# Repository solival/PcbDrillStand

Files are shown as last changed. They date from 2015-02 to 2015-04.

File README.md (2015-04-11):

# PCB Drill Press Stand
This is small neat drill press stand designed to use laser printer engines widely sold on ebay/aliexpress.
This project based on http://www.thingiverse.com/thing:144333 by Mark Benson design with next improvements:

- Designed for engine body sized L=35-60mm D=30mm
- Shifted base hole to center drill according new motor diameter
- Added 3x 3mm super light LED holders focused on drill working area
- Added PCB with voltage regulator and connector for standard notebook power unit (which is used for drill and light). This can be easily changed on any power source up to 24v (only connector should be changed in this case)
- Added holes in slider to mount PCB
- Added hole on left side of fixed sliding wedge for balancing spring/rubber.

Apart from that no big changes. I print gears with 40% filament and all other parts with 20% filament. Works fine.

This thing on thingiverse: http://www.thingiverse.com/thing:766712

# Photos
Drill Press Stand assembled

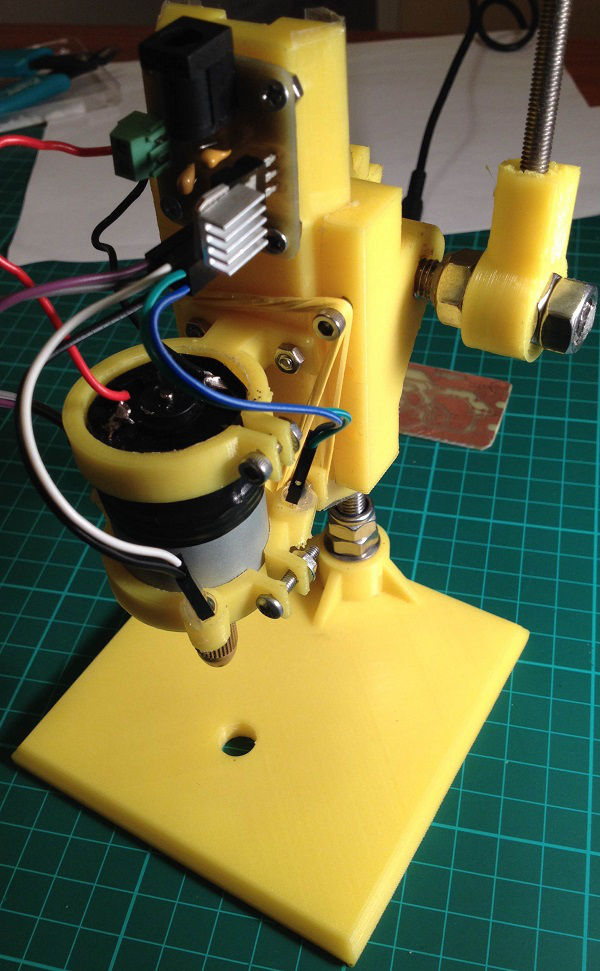
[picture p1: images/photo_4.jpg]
Drill press assembled

---

Drilling area light

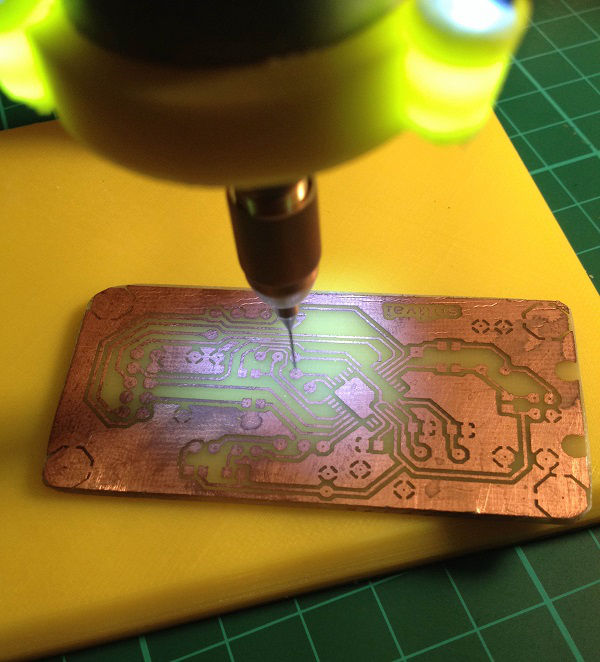
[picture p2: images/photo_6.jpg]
Drill Light

---

Assembled render front

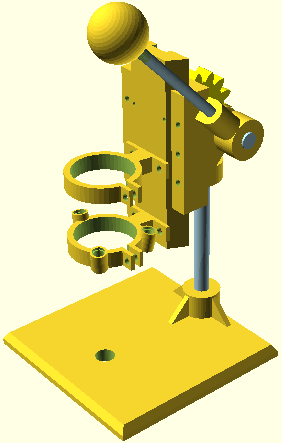
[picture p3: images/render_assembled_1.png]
Assembled Render

---

Assembled render back:

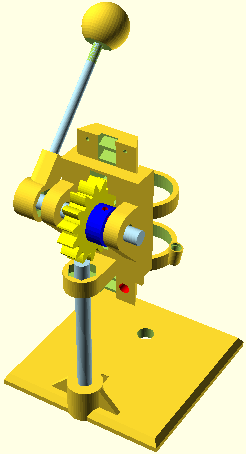
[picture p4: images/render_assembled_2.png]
Assembled Render

---

LED Light Schematics

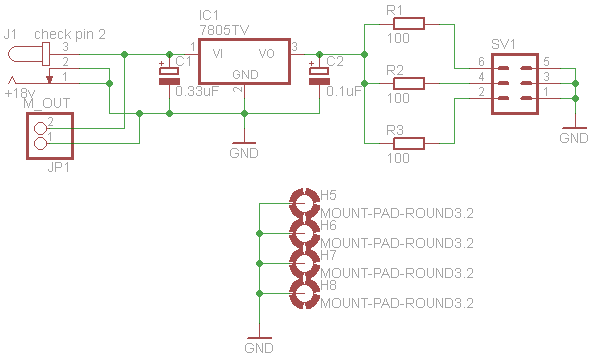
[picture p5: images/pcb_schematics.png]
Light schematics

---

LED Light board layout

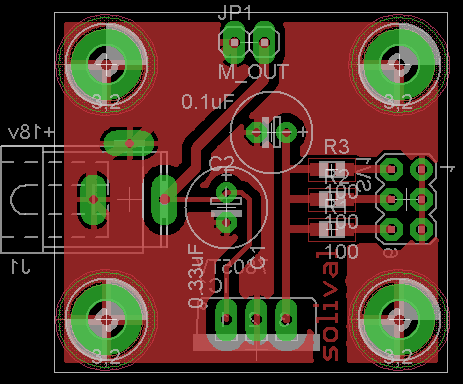
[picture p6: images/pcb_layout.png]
Light PCB layout


# Bill of Materials
## Mechanics
- ABS or PLA filament
- Drill chuck
- Threaded rod M5 (about 110mm)
- Threaded rod M8 (about 95mm and 80mm). One is for stand, second is for gear and fixed slider.
- 6x M8 nut, nyloc (better 8x for stand tightening)
- 4x 8mm washer
- 9x M3 18mm bolts
- 10x M3 nuts
- 6x 3mm washers
- 6x 3x12mm screws

## Electronics
- Motor from printer with body diameter 30mm and length between 35-60mm
- Female-Female du-pont wires 10cm (6x)
- 3x LED 3mm White
- 2.54mm 2-wire connector
- Jack plug (diameters must match your notebook power unit connector)
- Notebook power unit
- 2x3 pin header male
- LM7805 (or LM7812) voltage regulator
- 0.1uF and 0.33uF capacitors
- 3x 100 Ohm resistors (or 390 Ohm if LM7812 used)
- Prototype Board or etched PCB

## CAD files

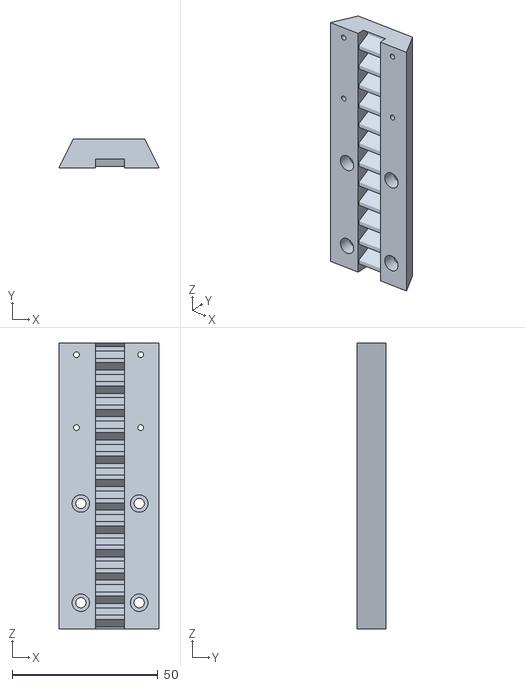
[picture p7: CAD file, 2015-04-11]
STL/sliding_wedge_rack.stl
34.3 x 9.80 x 98.0

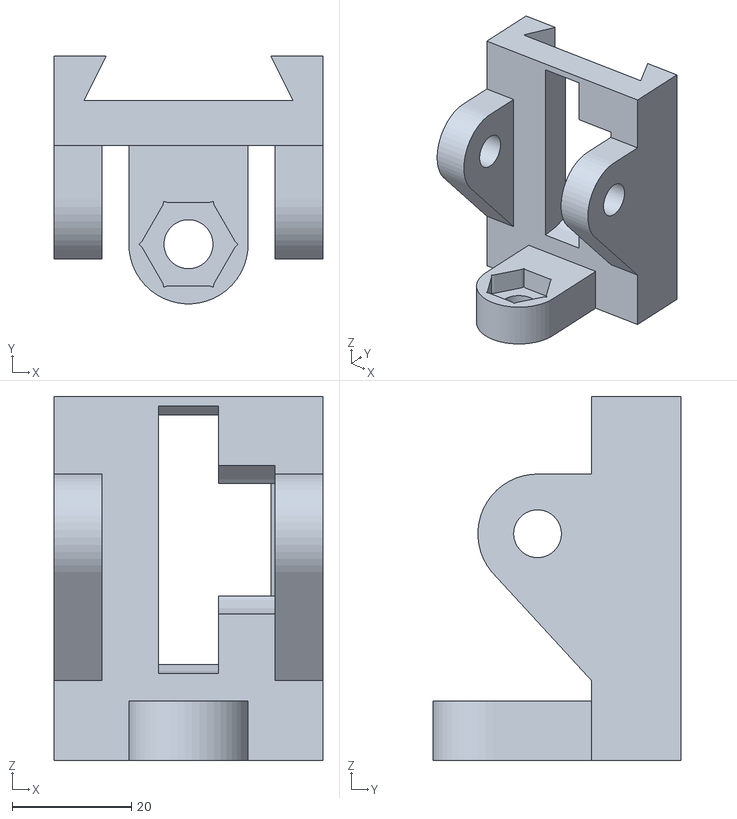
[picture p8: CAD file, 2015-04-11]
STL/fixed_slide.stl
45.0 x 41.5 x 61.0

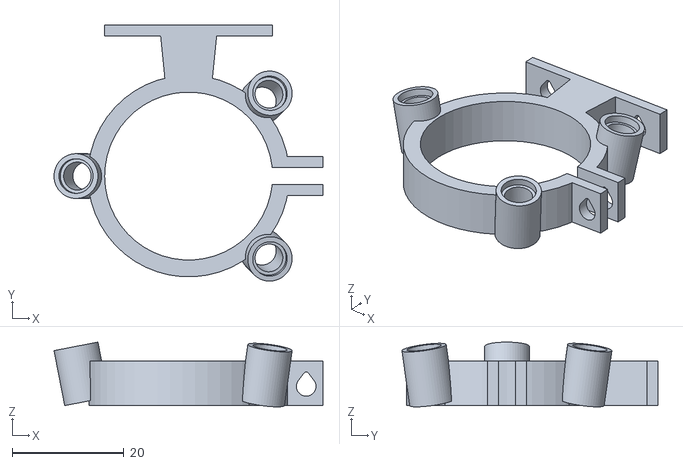
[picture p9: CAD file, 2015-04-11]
STL/rotacraft_rc18_drill_collar_mount.stl
48.1 x 45.8 x 11.6

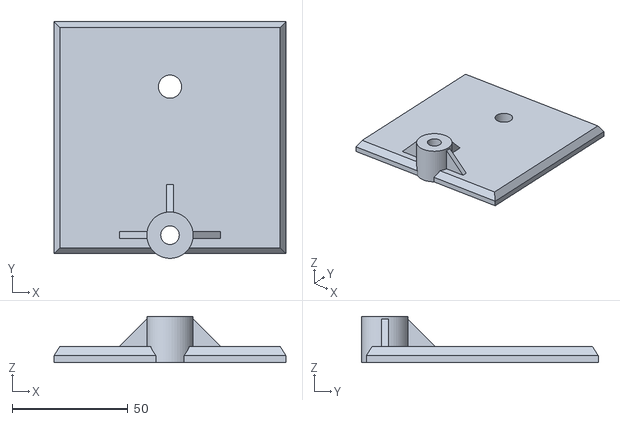
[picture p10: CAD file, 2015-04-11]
STL/drill_base.stl
100.0 x 102.0 x 20.0

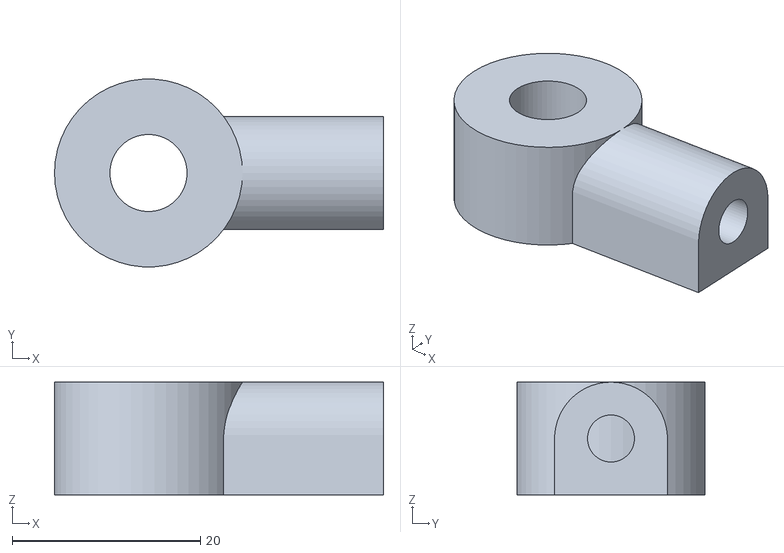
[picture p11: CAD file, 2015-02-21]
STL/arm_mount.stl
35.0 x 20.0 x 12.0

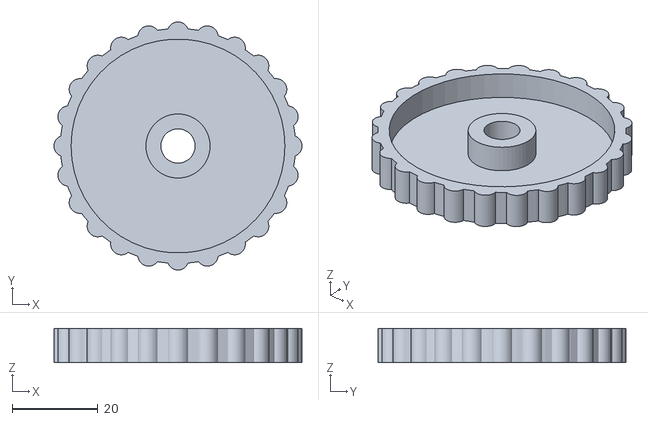
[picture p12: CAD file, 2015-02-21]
STL/thumb_wheel.stl
58.0 x 58.0 x 8.00

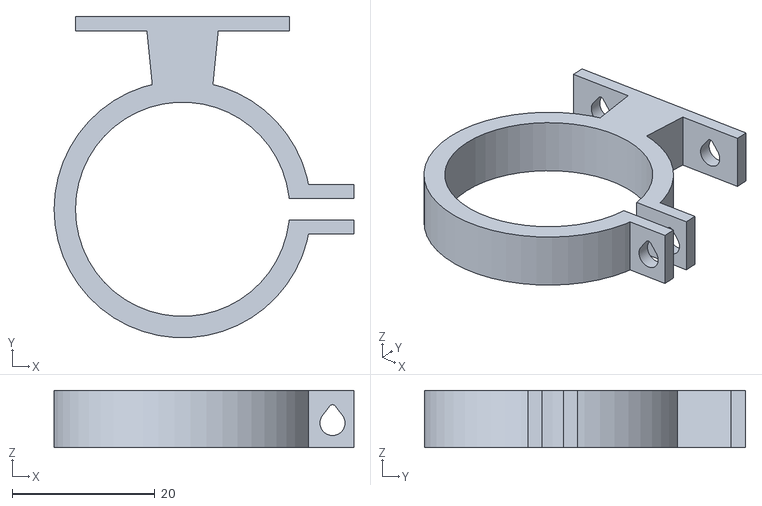
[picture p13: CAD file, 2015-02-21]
STL/rotacraft_rc18_drill_body_mount.stl
42.0 x 45.0 x 8.00

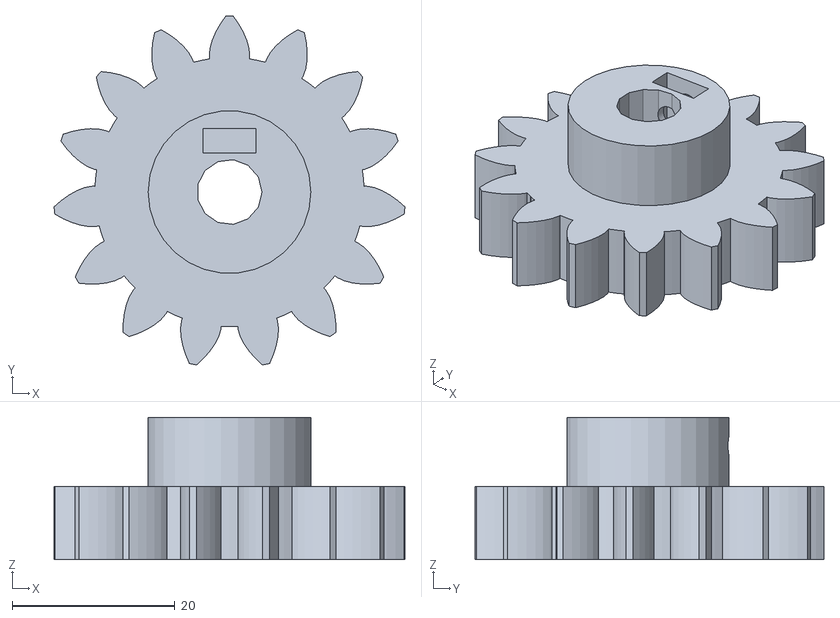
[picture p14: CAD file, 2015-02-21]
STL/rack_gear.stl
43.1 x 42.9 x 17.5

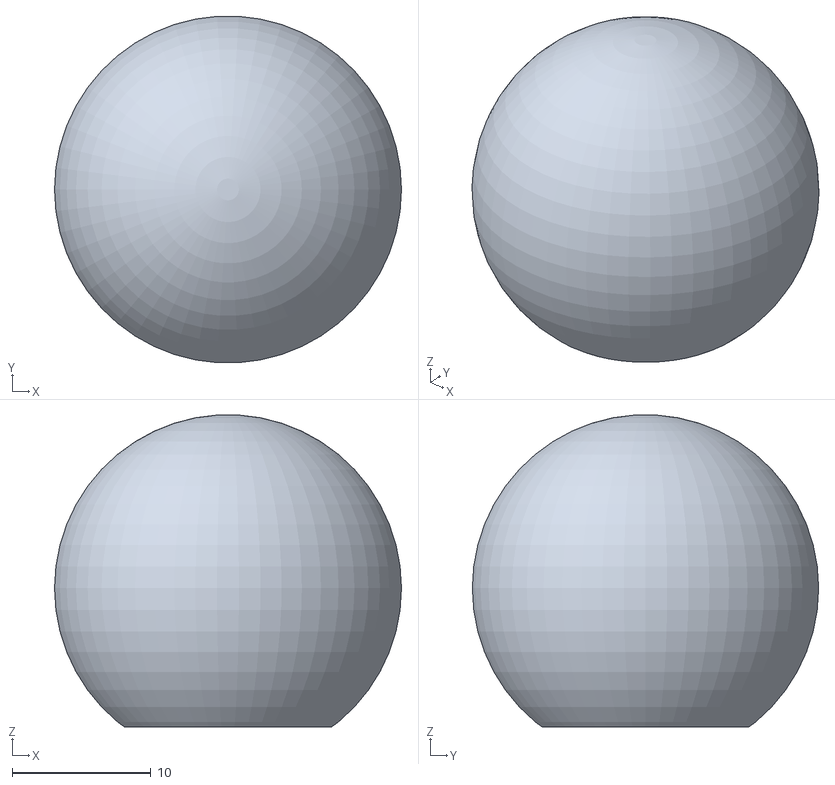
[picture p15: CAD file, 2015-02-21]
STL/arm_knob.stl
25.0 x 25.0 x 22.5

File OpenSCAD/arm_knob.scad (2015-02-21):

// PCB Drill Press for Hobby Drills
//
// Arm Knob for end of arm
//
// Copyright Mark Benson - Sept 2013
// 
// Licensed under:
// Creative Commons Attribution-NonCommercial-ShareAlike 3.0
//

// Call module here to render model for printing
// Comment out when calling from drill_press_assembly or you 
// will end up with two copies of the model.
//armKnob();

module armKnob()
{
	difference()
	{
		//Body
		sphere(r=25/2, $fn=50);
		
		//Flat on bottom of sphere
		translate([0,0,-12])
		cube([30,30,4], center=true);

		//Hole for M5 threaded rod		
		translate([0,0,-20])
		cylinder(r=5/2, h=30, $fn=50);
	}
}//End of armKnob()

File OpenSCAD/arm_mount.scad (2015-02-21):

// PCB Drill Press for Hobby Drills
//
// Arm mount
//
// Copyright Mark Benson - Sept 2013
// 
// Licensed under:
// Creative Commons Attribution-NonCommercial-ShareAlike 3.0
//

// Call module here to render model for printing
// Comment out when calling from drill_press_assembly or you 
// will end up with two copies of the model.
//armMount();

//Include Josef Prusas hardware functions lib for nut
include <functions.scad>;



module armMount()
{
	union()
	{
		difference()
		{
			//Arm mount centre
			translate([0,0,0])
			rotate([0,0,0])
			cylinder(r=20/2, h=12, $fn=50);
	
			//Cutout for M8 captive nut
			translate([0,0,-1])
			rotate([0,0,0])
			nut(13.5,6);
			
			//Cutout for M8 gear shaft
			translate([0,0,0])
			rotate([0,0,0])
			cylinder(r=8.2/2, h=30, $fn=50);
		}

		//Arm mount
		translate([0,0,0])
		rotate([0,0,0])
		difference()
		{
			hull()
			{
				//cylinder for m8 arm shaft
				translate([5,0,6])
				rotate([0,90,0])
				cylinder(r=12/2, h=20, $fn=50);
				
				//cube to give one side a flat for printing
				translate([15,0,0.5])
				rotate([0,0,0])
				cube([20,12,1], center=true);
			}

			//Cutout for M8 arm (should be a tight fit, heat shaft to fit or thread, of glue)
			translate([0,0,6])
			rotate([0,90,0])
			cylinder(r=5/2, h=40, $fn=50);

			//Cutout for M8 captive nut
			translate([0,0,-1])
			rotate([0,0,0])
			nut(13.5,6);
		}//End difference for arm mount
	}//End union for whole model
}//End module encapsulation

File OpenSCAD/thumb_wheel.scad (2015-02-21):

// PCB Drill Press for Hobby Drills
//
// Thumbwheel for turning shaft to move drill up and down
//
// Not used in final version - kept incase it is useful
//
// Copyright Mark Benson - Sept 2013
// 
// Licensed under:
// Creative Commons Attribution-NonCommercial-ShareAlike 3.0
//

// Call module here to render model for printing
// Comment out when calling from drill_press_assembly or you 
// will end up with two copies of the model.
//thumbWheel(thumbWheelDiameter, thumbWheelThickness, numberOfGrips, centreBossDiameter, centreBossHeight);

//Default values
thumbWheelDiameter = 55;
thumbWheelThickness = 8;
numberOfGrips = 24;
centreBossDiameter = 15;
centreBossHeight = 8;
shaftDiameter = 8;


module thumbWheel(thumbWheelDiameter, thumbWheelThickness, numberOfGrips, centreBossDiameter, centreBossHeight)
{
	union()
	{
		//Main body of thumbwheel
		difference()
		{
			//Outside of wheel
			translate([0,0,0])
			rotate([0,0,0])
			cylinder(r=thumbWheelDiameter/2, h=thumbWheelThickness, $fn=50);
			
			//Remove inside of wheel
			translate([0,0,2])
			rotate([0,0,0])
			cylinder(r=(thumbWheelDiameter-5)/2, h=thumbWheelThickness, $fn=50);

			//Remove shaft hole
			translate([0,0,-1])
			rotate([0,0,0])
			cylinder(r=shaftDiameter/2, h=centreBossHeight+2, $fn=50);
		}

		//Grips around outside of wheel
		difference()
		{
			//Distribute cylinders around the outside of wheel
			for ( x = [0:numberOfGrips-1])
			{
				rotate((x * 360)/numberOfGrips ,[0,0,1])
				translate([0,thumbWheelDiameter/2-1,0])
				cylinder(r=5/2, h=thumbWheelThickness, $fn=50);
			}
	
			//Remove the inside of the cylinders so it looks neat
			translate([0,0,2])
			rotate([0,0,0])
			cylinder(r=(thumbWheelDiameter-5)/2, h=thumbWheelThickness, $fn=50);
		}
	
		//Create the centre boss to mount the wheel on
		difference()
		{
			translate([0,0,0])
			rotate([0,0,0])
			cylinder(r=centreBossDiameter/2, h=centreBossHeight, $fn=50);

			//Remove shaft hole
			translate([0,0,-1])
			rotate([0,0,0])
			cylinder(r=shaftDiameter/2, h=centreBossHeight+2, $fn=50);
		}
	
	}//end of union
}//end of module

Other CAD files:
OpenSCAD/drill_base.scad
OpenSCAD/drill_press_assembly.scad
OpenSCAD/fixed_slide.scad
OpenSCAD/functions.scad
OpenSCAD/publicDomainGearV1.1.scad
OpenSCAD/rack_gear.scad
OpenSCAD/rotacraft_rc18_drill_body_mount.scad
OpenSCAD/rotacraft_rc18_drill_collar_mount.scad
OpenSCAD/sliding_wedge_rack.scad

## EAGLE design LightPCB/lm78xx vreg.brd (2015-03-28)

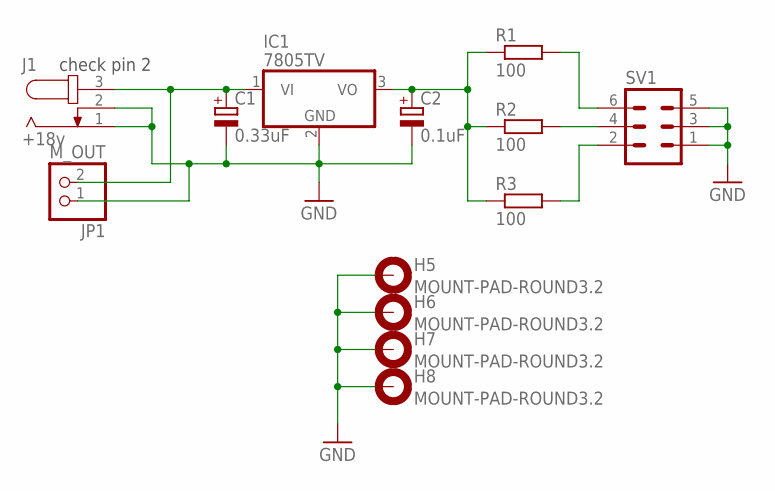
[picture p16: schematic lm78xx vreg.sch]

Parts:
C1: 0.33uF; E2,5-7
C2: 0.1uF; E2,5-7
H5, H6, H7, H8: MOUNT-PAD-ROUND3.2; 3,2-PAD
IC1: 7805TV; TO220V
J1: +18v; SPC4078
JP1: M_OUT; 1X02
R1, R2, R3: 100; R0805W
SV1: MA03-2

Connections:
GND: C1.-, C2.-, H5.B3,2, H6.B3,2, H7.B3,2, H8.B3,2, IC1.2 (GND), J1.1, J1.2, JP1.1, SV1.1, SV1.3, SV1.5
unnamed: C1.+, IC1.1 (VI), J1.3, JP1.2
unnamed: C2.+, IC1.3 (VO), R1.1, R2.1, R3.1
unnamed: R2.2, SV1.4
unnamed: R1.2, SV1.6
unnamed: R3.2, SV1.2

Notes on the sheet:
check pin 2

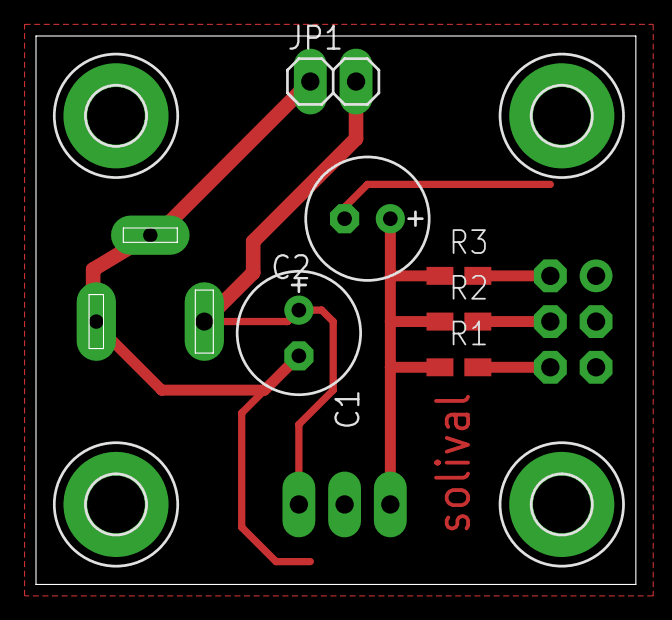
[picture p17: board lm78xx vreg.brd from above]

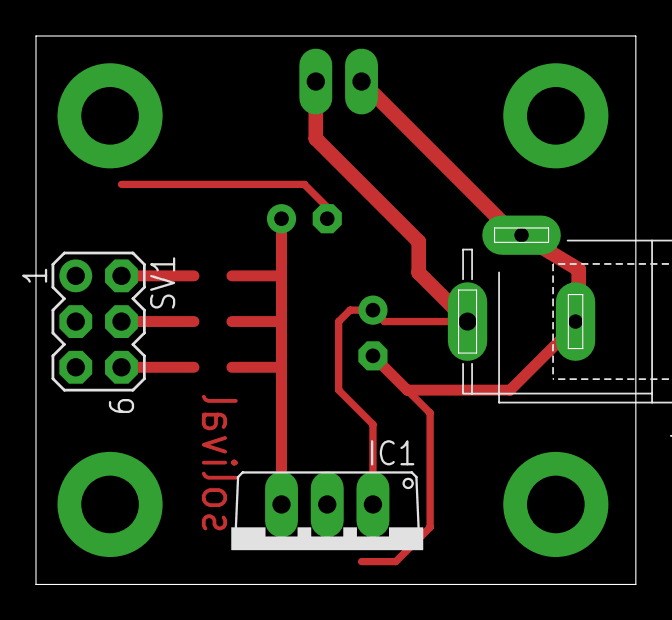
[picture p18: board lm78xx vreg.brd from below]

Board: 2 copper layers, 33.3 x 30.5 mm, 13 parts (3 on the bottom side), 6 nets.

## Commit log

2015-02-21 Initial commit
    All files that I have at the moment
    [arm_knob.scad, arm_knob.stl, arm_mount.scad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]
2015-03-11 Changed DRC for light PCB
    [lm78xx vreg.brd, lm78xx vreg.sch]
2015-03-28 Bigger distance between traces and ground pane.
    [lm78xx vreg.brd]
2015-04-11 PCB Rill Stand v1
    [drill_base.scad, drill_base.stl, fixed_slide.scad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]
